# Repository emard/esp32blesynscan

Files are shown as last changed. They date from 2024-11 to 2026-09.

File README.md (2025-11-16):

# ESP32 blesyncscan

Micropython ESP32, ESP32S3, ESP32C3 Bluetooth Low Energy (BLE)
Motor server, WiFi Motor Server and USB-WiFi Motor Client for
SynScan Pro on Windows, Linux, Android.
Arduino ESP32 Bluetooth Classic UART bridge for SynScan Pro
under Wine on Linux.
UART 3.3V TTL is connected to SkyWatcher Virtuoso Mini
or Virtuoso GTi mount.

ESP32C3 USB-C port can be used as direct USB-SERIAL on PC
connected to Motor over wire or remote USB-SERIAL over WiFi.

Do not use this to upgrade Motor firmware.
Motor firmware should be upgraded over wire using
USB-SERIAL UART 3.3V TTL based on PL2303 or FT232R chip.

# Install

"micropython" directory contains latest developent.
To install, continue with micropython/README.md

"Arduino" directory contains old code which should be
upgraded with features micropython code has.
To install, continue with Arduino/README.md

Bluetooth Classic is available only for Arduino.
Micropython doesn't support Bluetooth Classic.

# Electrical

There should be 12V->3.3V converter.
To save power recommended is switching converter 
(Canton Power or RECOM).
RJ-12 plug can't guarantee that GND makes
connection before 12V pin. Hot-plugging
can apply 12V to 3.3V pins and risk a
permanent damage. Avoid hot-plugging.

On the mount "Virtuoso Mini" RX and TX are labeled
swapped and seems as wired together making it a
half-duplex serial port and ESP32 should cancel echo.
ESP32 TX line should "simulate" open collector
output with a resistor 10k and small low drop diode
BAT42.

On the mount "Virtuoso GTi" RX and TX are labeled
normal and are not wired together making it a
full-duplex serial port without echo.
ESP32 TX line should connect directly to ESP32.

In the mount manual see RJ-12 pinout.
Conenct RJ-12 RX/TX with short straight
RJ-12 cable to ESP32 RX2/TX2 pins.

# Schematics

First prototype (ESP32)

                 Canton Power
                ┌─────────────┐
                │IN        OUT│
                │12V  GND 3.3V│
                └─────────────┘
                  │    │    │
      MOUNT       │    │    └───────────────┐
     MINI/GTi     │    │                    │   ESP32
    ┌───────┐     │    │                    │  ┌───────┐
    │    12V│─────┘    │         10k/BAT42  └──│3.3V   │
    │       │          │         ┌─░░░░─┐      │       │
    │     TX│──────────│─────────┼──>∫──┴──────│TXD    │
    │       │          │         └─────────────│TX     │
    │     RX│──────────│───────────────────────│RX     │
    │       │          │                       │       │
    │    GND│──────────┴───────────────────────│GND    │
    └───────┘                                  └───────┘

Minimal schematic (ESP32S3) old

                     RECOM
                 R-78K3.3-0.5
                ┌─────────────┐
                │12V  GND 3.3V│
                │IN        OUT│
                └─────────────┘
                  │    │    │
      MOUNT       │    │    └─────────┐
     MINI/GTi     │    │              │   ESP32S3
    ┌───────┐     │    │              │  ┌───────┐
    │    12V│─────┘    │   10k/BAT42  └──│3.3V   │
    │       │          │    ┌─░░░░─┐     │       │
    │     TX│──────────│────┼──>∫──┴─────│TXD    │
    │       │          │    └────────────│TX     │
    │     RX│──────────│─────────────────│RX     │
    │       │          │                 │       │
    │    GND│──────────┴─────────────────│GND    │
    └───────┘                            └───────┘

Minimal schematic (ESP32S3) new

                     RECOM
                 R-78K3.3-0.5
                ┌─────────────┐
                │12V  GND 3.3V│
                │IN        OUT│
                └─────────────┘
                  │    │    │
      MOUNT       │    │    └─────────┐
     MINI/GTi     │    │              │   ESP32S3
    ┌───────┐     │    │   10k/BAT42  │  ┌───────┐
    │    12V│─────┘    │    ┌─░░░░─┐  └──│3.3V   │
    │       │          │    ├──>∫──┴─────│TXD    │
    │     TX│──────────│────┴────────────│TX     │
    │       │          │    ┌─░░░░─┐     │       │
    │     RX│──────────│────┼──>∫──┴─────│RXD    │
    │       │          │    └────────────│RX     │
    │    GND│──────────┴─────────────────│GND    │
    └───────┘                            └───────┘

part numbers and pinouts

    RJ-11 or RJ-12 Connector
    Mouser P/N: 538-95501-2661   0.5$
    Mouser P/N: 523-RJE031660310 1$
    Mouser P/N: 490-CRJ051-1-TH  2$

      RJ-12         RJ-11
    ┌────────┐    ┌────────┐
    │ 123456 │    │  2345  │
    │        │    │        │
    └──┐  ┌──┘    └──┐  ┌──┘
       └──┘          └──┘
    front view    front view

    1        N.C.
    2 yellow TX       (3.3V) (esp32 sends to "Mini", receives from "GTi")
    3 green  Vpp+     ( 12V) (esp32 draws power)
    4 red    RX       (3.3V) (esp32 receives from "Mini", sends to "GTi")
    5 black  GND
    6        N.N.

    Voltage converter 4.5-36V -> 3.3V
    Mouser P/N: 919-R-78K3.3-0.5 7$

                     RECOM 
                 R-78K3.3-0.5
                ┌─────────────┐
             IN │12V  GND 3.3V│ OUT
                │             │
                │             │
                └─────────────┘
                  bottom view

    XIAO ESP32S3 MINI old
    Mouser P/N: 713-113991114    7$

                 XIAO  ESP32S3
                ┌─────────────┐
                │1    USB   5V│
                │2         GND│
                │3        3.3V│
                │4           9│
                │5           8│
                │6  TX       7│
                │43 TXD  RX 44│
                └─────────────┘
                    top view

    XIAO ESP32C3 MINI old
    Mouser P/N: 713-113991054    5$

                 XIAO  ESP32C3
                ┌─────────────┐
                │2    USB   5V│
                │3         GND│
                │4        3.3V│
                │5          10│
                │6           9│
                │7  TX       8│
                │21 TXD  RX 20│
                └─────────────┘
                    top view

    XIAO ESP32S3 MINI new
    Mouser P/N: 713-113991114    7$

                 XIAO  ESP32S3
                ┌─────────────┐
                │1    USB   5V│
                │2         GND│
                │3        3.3V│
                │4           9│
                │5           8│
                │6  TXD  RXD 7│
                │43 TX   RX 44│
                └─────────────┘
                    top view

    XIAO ESP32C3 MINI new
    Mouser P/N: 713-113991054    5$

                 XIAO  ESP32C3
                ┌─────────────┐
                │2    USB   5V│
                │3         GND│
                │4        3.3V│
                │5          10│
                │6           9│
                │7  TXD  RXD 8│
                │21 TX   RX 20│
                └─────────────┘
                    top view

# Connection

Looking at female RJ-12 socket on the mount:

    ┌────────┐
    │ 123456 │
    │        │
    └──┐  ┌──┘
       └──┘

    1 blue   N.C.
    2 yellow TX       (3.3V) (mount "Mini" receives, "GTi" sends)
    3 green  Vpp+     ( 12V) (mount provides power)
    4 red    RX       (3.3V) (mount "Mini" sends, "GTi" receives)
    5 black  GND
    6 white  Reserved (3.3V)

RX/TX roles on the mount "Virtuoso Mini" are swapped and
actually indicate RX2/TX2 on ESP32.

    Virtuoso Mini  ESP32
    -------------  ----------
    2 yellow TX    TX2 GPIO17 (over resistor/diode)
    4 red    RX    RX2 GPIO16
    5 black  GND   GND

RX/TX roles on the mount "Virtuoso GTi" are labeled normal,
here we swap TX2/RX2 on ESP32.

    Virtuoso GTi   ESP32
    ------------   ----------
    2 yellow TX    RX2 GPIO17 (direct)
    4 red    RX    TX2 GPIO16
    5 black  GND   GND

RJ-11 4-pin socket can be used instead of
RJ-12 6-pin because pins 1 and 6 are not connected.

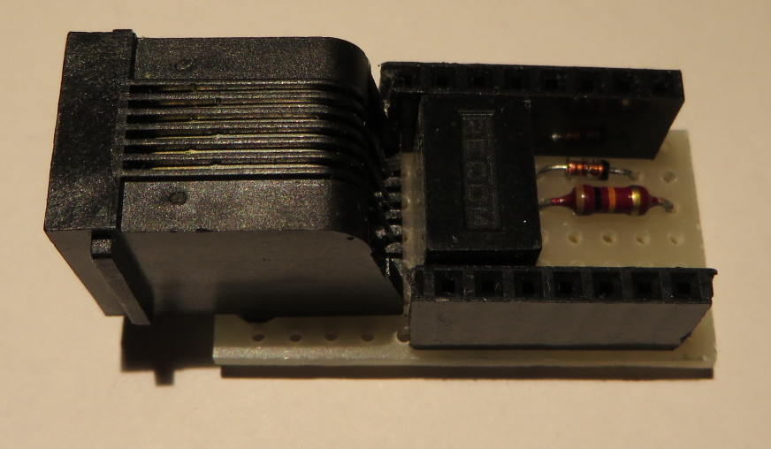
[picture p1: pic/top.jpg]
top


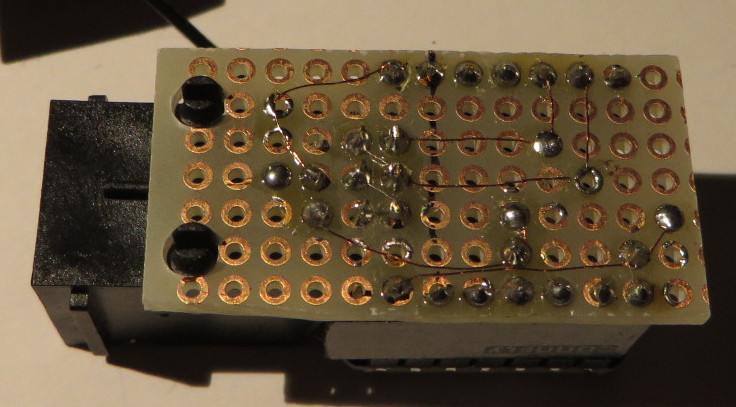
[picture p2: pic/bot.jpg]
bot


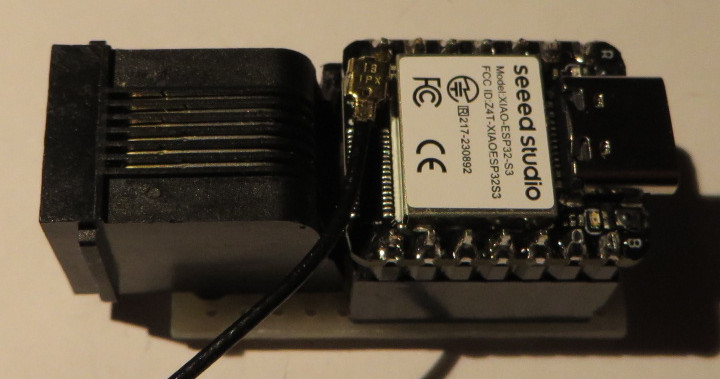
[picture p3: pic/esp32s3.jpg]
esp32s3


# WARNING WARNING WARNING

RJ12 pinout on the adapter matches the pinout
on the mount, so the "straight" wired cable
should be used.

There are different RJ-11 and RJ-12 cables,
with [straight and cross wiring](/doc/straight-vs-cross-cable.pdf).
For the telephones it does not matter but here it matters!

STANDARD PHONE CROSS CABLE MAY NOT BE SUITABLE.
USE ONLY STRAIGHT WIRED 4-PIN RJ-11 or
STRAIGHT WIRED 6-PIN RJ-12. CROSS RJ-11 AND RJ-12 
CABLES AND ALL 2-PIN RJ-11 CABLES ARE NOT SUITABLE.
IF A CROSS WIRED CABLE OR ANY 2-PIN CABLE IS CONNECTED
THEN 12V WILL FRY ELECTRONICS IN THE MOUNT AND ESP32.

# Bluetooth Classic or Low Energy

After board power ON or reset by pressing "EN" button,
blue LED will turn ON for 1.5 seconds.

By default if nothing is pressed ESP32 provides
Bluetooth Low Energy Serial.

If "BOOT" button is held during blue LED is ON
then ESP32 will provide Bluetooth Classic Serial.

ESP32 in Bluetooth Low Energy mode only supports
BLE protocol and does not save battery power.
In both Classic and Low Energy modes ESP32 consumes
about 70 mA.

# Android

Synscan works in BLE mode.

SynScan pro -> Settings -> Connection Settings -> BLE

If device no longer appears in connect list and 
you want to retry connecting, then android application
has to be stopped and started again:

View applications as smaller windows. To stop SynScan,
drag it left on ardoid 10 or drag it up on android 14.

Protocol testing:

"Serial Bluetooth Terminal" can connect in
Bluetooth Classic directly when ESP32 is booted
in Bluetooth Classic mode.

"Serial Bluetooth Terminal" can connect in
Low Energy mode with long touch on SynScan_BLE device
selecting "Edit" Custom profile and then
accepting offered UUID values for Service, Read and Write.
Settings:

    Receive Newline = CR
    Send    Newline = Auto (Same as Receive)
    Send    Local Echo ( o) enabled

Basic request/response works:

    request
    :e1\r

    response
    =0210A1\r

# Linux Bluetooth Classic

Bluetooth classic works from linux and
SynScan 2.5.2 pro running under wine,
connecting as serial port.

in shell 1

    hcitool scan
    Scanning ...
            24:0A:C4:11:22:33   SynScan_BT
    rfcomm bind /dev/rfcomm0 24:0A:C4:11:22:33
    unzip synscanpro_windows_252.zip
    cd SynScanPro
    wine SynScanPro.exe
    ... wine will initialize com1 as symlink to /dev/ttyS0
    ... we must change this symlink to /dev/rfcomm0

in shell 2

    cd ~/.wine/dosdevices
    ln -sf /dev/rfcomm0 com1

in SynScan Pro window 

    ... SynScan pro -> Settings -> Connect Settings -> Serial
    ... Serial Port: COM1
    ... press top "<" touch btn then "Connect" btn will appear.
    ... touch "Connect" btn, retry few times

SynScanPro can be debugged from wine:

    winedbg --gdb SynScanPro.exe
    ...
    Wine-gdb> c

# Linux Bluetooth Low Energy

Bluetooth low energy works from linux and
SynScan 2.5.2 pro running under wine,
connecting as serial port.

It works over ble-serial if esp32 is emulating
BLE nRF chip. RN4871 chip emulation will not be
detected by ble-serial.

Install
    
    https://github.com/Jakeler/ble-serial

in shell 1

    source ble-venv/bin/activate
    ble-scan -i hci1
            24:0A:C4:11:22:33   SynScan_BLE
    ble-serial -i hci1 -d 24:0A:C4:11:22:33
    (ble-venv) guest@nuc1:~$ ble-serial -i hci1 -d 24:0A:C4:11:22:33
    23:38:03.521 | INFO | linux_pty.py: Port endpoint created on /tmp/ttyBLE -> /dev/pts/2
    23:38:03.521 | INFO | ble_interface.py: Receiver set up
    23:38:03.741 | INFO | ble_interface.py: Trying to connect with 24:0A:C4:11:22:33: SynScan_BLE
    23:38:05.443 | INFO | ble_interface.py: Device 24:0A:C4:11:22:33 connected
    23:38:05.443 | INFO | ble_interface.py: Found write characteristic 6e400002-b5a3-f393-e0a9-e50e24dcca9e (H. 44)
    23:38:05.443 | INFO | ble_interface.py: Found notify characteristic 6e400003-b5a3-f393-e0a9-e50e24dcca9e (H. 41)
    23:38:05.826 | INFO | main.py: Running main loop!

in shell 2

    cd SynScanPro
    wine SynScanPro.exe
    ... wine will initialize com1 as symlink to /dev/ttyS0
    ... we must change this symlink to /dev/rfcomm0

in shell 3

    cd ~/.wine/dosdevices
    ln -sf /tmp/ttyBLE com1

in SynScan Pro window 

    ... SynScan pro -> Settings -> Connect Settings -> Serial
    ... Serial Port: COM1
    ... press top "<" touch btn then "Connect" btn will appear.
    ... touch "Connect" btn, retry few times

SynScanPro can be debugged from wine:

    winedbg --gdb SynScanPro.exe
    ...
    Wine-gdb> c

# Windows

With suitable BLE adapter, for example TP-LINK UB500
SynScan pro 2.5.2 for windows connects with "SynScan_BLE".

"SimplySerial" is simple terminal emulator for
windows. It can can be started from powershell
to print debug messages from esp32.

    ./ss -com:8 -baud:9600
    Connected
    Disconnected

# Principle of operation

ESP32 creates a bluetooth server with serial port bridge.
Phyisical TTL serial port should be 9600,8,n,1. Using 9800
baud seems to receive less noise than 9600 baud.

Minimum that works is a BLE Service (UUID 0xA002) with
two characteristics, one for RX other for TX:

RX Direction SynScan->motor (UUID 0xC302)

Bluetooth LE packetizes serial protocol so
entire message is delivered in one packet.
ESP32 filters out some problematic commands for
"2.16.A1" motor firmware (see Firmware bugfix)
other firmwares may not need it.
Message is written to TTL serial and signaled
with "NOTIFY" flow control.

TX Direction motor->SynScan (UUID 0xC306)

TTL serial receiver buffers bytes until "complete"
message is received, it begins with '=' or '!'
and ends with '\r'. It is delivered via bluetooth
and signaled with "INDICATE" flow control.

# TTL Serial Port

Mount's serial TTL port is half-duplex
and it seems that mount has hardware
loopback. So everything that esp32 sends
to the mount, the mount immediately echoes it.

In the code there is echo cancellation built in
to reduce BLE traffic, run faster and save energy.

Mount and ESP32 cannot send at the
same time. If ESP32 tries to send
while mount sends, then the data
received by ESP32 will be just noise.

Received bytes are occasionaly wrong
with typically one of the bits that
should be 0 errorenously received as 1.
This happens less often when mount is
just powered one and more often after
alignment when mount is driving motors
for tracking.

# Firmware bugfix

Motor firmware version 2.16.A1 is the latest but has
problem with SynScan application on android.
After each connect user must enable "Auxiliary Encoder"
otherwise mount will start turning around azimuth axis
and will never stop by itself (user should press cancel to stop).

According to
[BDN at Cloudy Nights](https://www.cloudynights.com/topic/941083-skywatcher-heritage-90-virtuoso-synscan-pro-compatibility/)
this bug can be fixed by making USB-SERIAL adapter and flashing firmware
[MC006_Tracking_V0216.MCF](https://stargazerslounge.com/topic/336944-firmware-for-the-virtuoso-skywatcher/)
posted by Antoine1997 at Stargazer's Lounge.

Although this firmware also has version 2.16.A1 it
is different and fixes the encoders problem. Warning
flashing firmware using WiFi dongle will brick the board and
should never be tried, so use only usb-serial.

If you are not comfortable with flashing the firmware,
here is the fix that forces using Auxiliary encoders.

fix#1: in function "udpcb()" one message is rewritten
with this fix Auxiliary Encoder doesn't have to be enabled.
It seems that mount internally always uses Auxiliary Encoders.
Regardless of Auxiliary Encoders being set ON or OFF without
this patch, when clutches are released and mount is manually moved,
SynScan always knows its new position.

    :W2050000\r -> :W2040000\r

fix#2: prevents sending junk to motor firmware which
is easy to crash.

SynScan sends some AT command probably for its
original SynScan WiFi ESP8266 AT firmware.
This AT command should not reach motor firmware so
"udpcb()" function rewrites this AT command as ":e1\\r"
and to this command motor firmware responds with
version number which is not really response to AT
command but SynScan accepts it.

    AT+CWMODE_CUR?\r\n -> :e1\r

fix#3: receive buffer is discarded after timeout of 10 ms
or when unexpected (noise) byte is received outside of
expected chars "=0123456789ABCDEF!\r". Synscan will
retry the command after its own timeout.
This fix improves initial connect, without this fix
and without open collector fit with diode and resistor,
SynScan sometimes needs to be manually restarted few
times to connect.

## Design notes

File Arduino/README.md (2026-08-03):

# Install

"esp32/btblesynscan" supports both Bluetooth
Classic and Bluetooth Low Energy on ESP32.
"esp32s3" supports Bluetooth Low Energy on ESP32S3.

From board manager Install esp32 by espressif.
Select board "ESP32 Dev Module" or "XIAO_ESP32S3".

Copy "btblesynscan.ino" to directory "~Arduino/esp32blesynscan/btblesynscan/btblesynscan.ino"
Copy "esp32s3.ino" to directory "~Arduino/esp32blesynscan/esp32s3/esp32s3.ino"

From Arduino, open project "~/Arduino/esp32blesynscan/btblesynscan",
or "~/Arduino/esp32blesynscan/esp32s3"
compile and upload to ESP32 board connected with Micro USB Cable (ESP32)
or USB-C Cable (ESP32S3).

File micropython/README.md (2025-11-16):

# SynScan_BLE Micropython version

300 lines of micropython replace
parts of synscan protocol on transmit
and receive side to:

Slow speed for encoders to reliably
track position without loosing counts.

Fine tune counts per revolution.
Turning both axes for 180° should
point to the same object as 0°.

Fake version number for synscan
to avoid using long X-commands.

# Install

    mpremote cp synscan_cfg.py synscan.py main.py :/

# Configure

Almost everything is configurable. Edit

    synscan_cfg.py

Using your favourite text editor on PC.
ESP32 has good editor written in micropython.

# Onboard Editor

ESP32 can run small [VT100 terminal editor](https://github.com/robert-hh/Micropython-Editor)

Automatic install from internet using mpremote mip:

    mpremote mip install github:robert-hh/Micropython-Editor

Edit config file:

    >>> from pye import pye
    >>> pye("synscan_cfg.py")

quick editor help

    ctrl-q        quit
    ctrl-s        save
    backspace     delete left of cursor
    arrows        move cursor
    shift-arrows  select block
    del           delete selected block
    ctrl-c        copy   selected block
    ctrl-v        paste  selected block
    ctrl-e        redraw screen

Troubleshooting

ESP32-WROOM and ESP32C3 dont have PSRAM so
memory is tight. After "import synscan"
there will be not enough free memory to
load editor:

    >>> from pye import pye
    Traceback (most recent call last):
      File "<stdin>", line 1, in <module>
    MemoryError: memory allocation failed, allocating 285 bytes

workaround: Get micropython prompt with ctrl-c, then
while holding ctrl type quickly "dccc" to soft reboot
and immediately interrupt "main.py" before
"import synscan". It should be possible to
load editor then:

    ctrl-c
    ...
    >>>
    ctrl-dccc
    ...
    >>> from pye import pye
    >>> pye("synscan_cfg.py")

# BLE Motor Server

Primary use is for Android. Works on Windows.
Linux BLE-serial written in python doesn't work.
Mount lacks BLE support and using its WiFi
is not practical, complicated routing etc.

BLE connects in few seconds, works stable and reliable.
WiFi on android is free to be used for internet
access or camera.

Works on ESP32, ESP32S3, ESP32C3.

When BLE receives request from synscan,
it sends it over UART and waits some timeout 30 ms or 200 ms
for UART response. Received response
is sent back to synscan. 

UART should send someting to motor hardware
to get response. Motor hardware is otherwise quiet.

# WiFi Motor Server

Primary use is to make additional networking
connectivity and compatibility. It can be WiFi
client while mount is WiFi Server.

Works on ESP32, ESP32C3.

To print IP

    synscan.wifi.ifconfig()

Currently it doesn't work reliable on ESP32S3.
Multiple retries required to connect. Packet loss
and timeout too long to be practical (30 seconds).

# WiFi to USB-Serial Motor Client

Primary use is for linux. Works on Windows and Android too.
Linux BLE-serial written in python doesn't work so this USB
to WiFi bridge is very practical.
ESP32 connects to mount using WiFi
and modifies protocol to fix issues.

Works on ESP32, ESP32S3, ESP32C3 (wine reboots ESP32C3).
Micropython versions from 1.23.0 to 1.26.1 have been
tried but ESP32S3 doesn't connect to WiFi.

Android: SynScan Pro connects with default serial settings

    SynScan Pro > Settings > Connection Settings > Serial

Linux: SynScan Pro works under wine when you find COM port
and set serial read timeout to 3-5 seconds.

To find out which serial port on wine is for synscan:

    ls -al ~/.wine/dosdevices
    lrwxrwxrwx 1 user user   12 Oct  10 23:52 com5 -> /dev/ttyACM0

Port is COM5 (last number can vary).

Wine SynScan Pro needs increased serial parameters to connect:

    Resend Tries * Serial Read Timeout > 9 seconds

ESP32S3 connects with default serial timeouts.

ESP32C3 needs increased serial timeouts.
When Synscan initiates connection to serial port it
probably toggles DTR or does something to serial port
which causes ESP32C3 to restart.
Read timeout should be long enough for
ESP32C3 to boot and connect to mount WiFi.

    SynScan Pro > Settings > Connection Settings > Serial
    SynScan Pro > Settings > Connection Settings > Resend Tries      > 2
    SynScan Pro > Settings > Connection Settings > Read Timeout (ms) > 5000

or

    SynScan Pro > Settings > Connection Settings > Serial
    SynScan Pro > Settings > Connection Settings > Resend Tries      > 10
    SynScan Pro > Settings > Connection Settings > Read Timeout (ms) > 1000

# Direct Wire USB-Serial Motor Client

Works on Windows, Android, Linux.
Works on ESP32, ESP32S3, ESP32C3 (wine reboots ESP32C3).
Similar as WiFi to USB-Serial Motor Client.

# Troubleshooting

Virtuoso Mini with MC006:

According to
[BDN at Cloudy Nights](https://www.cloudynights.com/topic/941083-skywatcher-heritage-90-virtuoso-synscan-pro-compatibility/)
this bug can be fixed by making USB-SERIAL adapter and flashing firmware
[MC006_Tracking_V0216.MCF](https://stargazerslounge.com/topic/336944-firmware-for-the-virtuoso-skywatcher/)
posted by Antoine1997 at Stargazer's Lounge.

Virtuoso GTi with MC014:

Flash firmware 3.40.AF but and synscan_cfg.py has
appropriate fixes, this includes slowing down manual
and goto slew, adjusting number of pulses per revolution
and rewriting firmware version to 3.36.AF to avoid using
of new X-commands.

CPU of MC014 misses encoder pulses, it is probably because
interrupt is used to count pulses instead of using hardware
counting like PCNT on ESP32 which may also be available on ESP8266.
which is mounted on MC014 PCB.

Best is to avoid switching to aux controllers during first 15 minutes,
while WiFi LED on the mount is blinking.
After 15 minutes WiFi LED will turn ON constantly, WiFi will be
off and interrupts will have more chance to catch encoder pulses.
so then it is good time to try aux encoders.

Encoders will then correctly work when synscan commands are send
from application to the mount and mount is moving slow according
to synscan_cfg.py slew speed setup.

But when clutches are released for manually pointing telescope
aka "Freedom Find" mode then aux controllers will start
loosing counts and that means that "Freedom Find" actually
doesn't work for MC014 hardware with currently tried firmwares
3.36.AF and 3.40.AF.

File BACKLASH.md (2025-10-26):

# Backlash Reduction

Backlash is annoying accumulated mechanical energy
in motor tranmission which visually manifests as
telescope first goes a few arc minutes in counter
direction than it goes in correct direction.

Backlash can be reduced to be almost visually
unnoticeable by precisely adjusting distance
between worm and sprocket wheel.

Tools required:

    Phillips screwdriver PH1
    Flat long screwdriver
    L-shaped Hex Allen wrench 2 mm
    Fork-shaped Hex nut wrench 7 mm

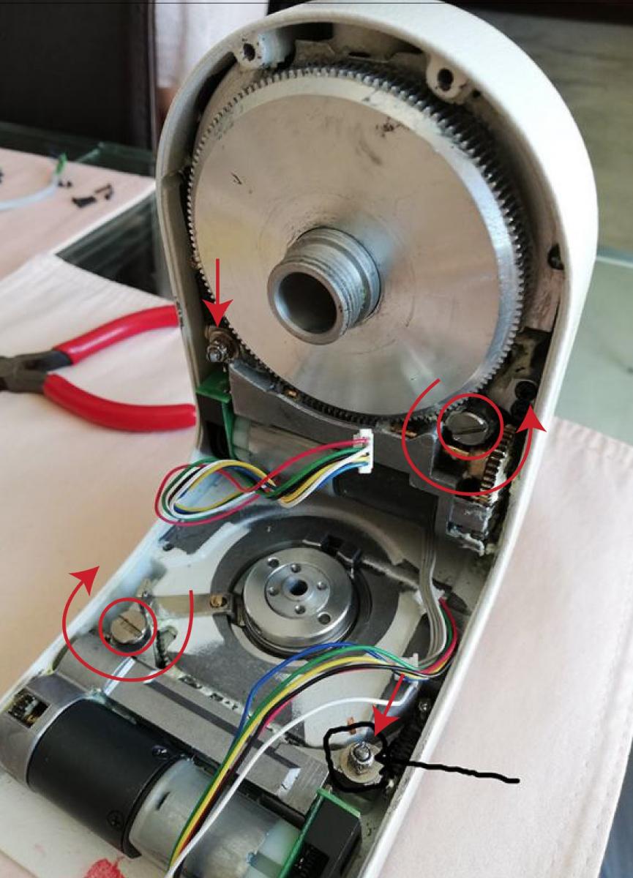
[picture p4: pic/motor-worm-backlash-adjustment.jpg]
backlash


Backlash can be adjusted by minimal disassembly,
no wires need to be removed but hood has to be
released carefully and held by hands while unscrewing
big screws while being very gentle with wires.

With long flat screwdriver release the big cylindrical
flat screw by turning 180° counter-clockwise.
On the picture this flat screw is marked by red circle.

Not visible on the picture is a smaller black screw
touching the big screw, this screw has hex hole for
2 mm Allen wrench and is fixed in place by counter-tightened
7 mm nut which is additionaly fixed with lacquer.

With Hex Fork wrench and Hex Allen wrench break the
lacquer and release hex nut to allow some space for
adjustment, like 1 mm.

Partially assemble the mount to leave hood open for
access with Hex Allen wrench and to have neccesary
parts in place to hold the telescope tube. Launch
motor control software, set software backlash
correction to zero and use cursors to move telescope
by visually monitoring backlash.

Change distance of the worm from sprocket wheel
by turning the black screw with Hex Allen wrench
until backlash disappears.

That,s it! After carefully tightening and assembling
check that everying is still working.

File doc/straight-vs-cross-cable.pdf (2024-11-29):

For cables with RJ-11 connectors, the terminology “Straight-through” and “Reverse” are often confused.

When one of these cables is considered “straight-through”, it means that when looking at both connectors side-by-side, the colors of the internal wires match (as shown below).

This is often mistaken as “straight-through”, mainly due to fact that if you were to stretch the cable out, the wires would stay side by side the whole length without going over each other. This, however, is incorrect.

For telephone systems, this doesn’t make a difference. However, when these cables are used for other means, such as personal projects, in various nonstandard uses, or other DIY-type instances, this difference is often important.

When it is “reverse,” however, the wires are mirrored (as shown below).

non-standard

standard

## RJ-11 CONNECTOR STRAIGHT-THROUGH (non-standard) vs. REVERSE (standard) EXPLANATION

(Hook is underneath)

RJ11 Plug

(Hook is underneath) (Hook is underneath)

RJ11 Plug

(Hook is underneath) (Hook is underneath)

(Hook is underneath)

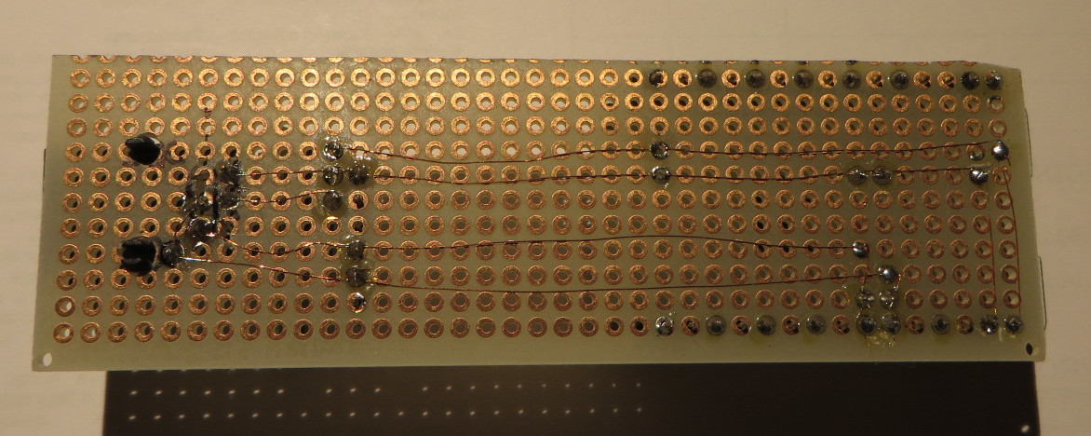
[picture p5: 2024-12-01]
pic/prototype-bot.jpg

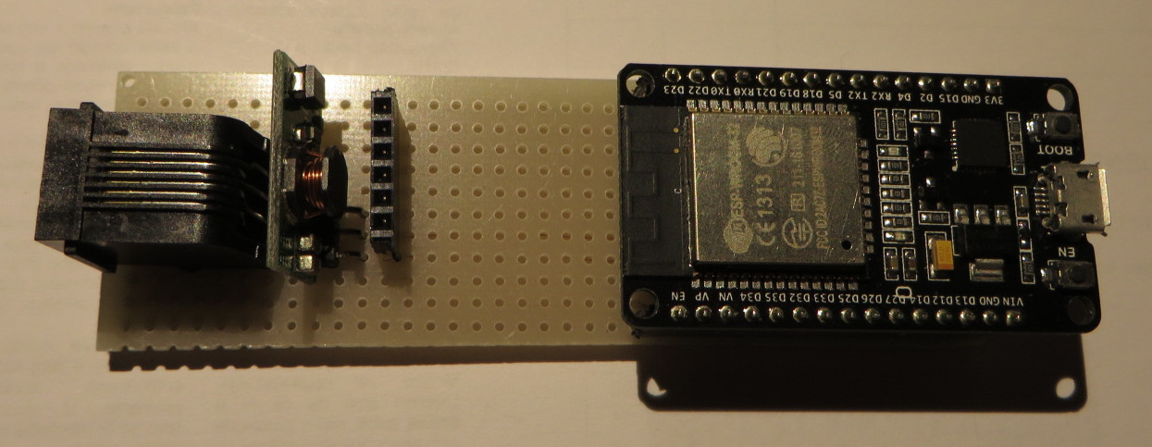
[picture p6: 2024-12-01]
pic/prototype-top.jpg

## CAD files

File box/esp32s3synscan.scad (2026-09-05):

// box to insert pcb and fix with 2 screws

pcb_size = [19,41,1.6]; // size of PCB

box_inner = [22,42,21+2.5];
thick = 2;

rail_top   = [2,42,2];
rail_bot   = [2.5,42,2];
rail_spc   = 2.5;

pcb_bottom = 2.5+3; // space from bottom
usb_pos = 14; // from PCB bottom

module pcb()
{
  translate([0,-thick,box_inner[2]/2-rail_bot[2]/2-pcb_bottom])
  cube(pcb_size,center=true);
}

module rounded_cube(v,r)
{
  minkowski()
  {
    h_minkowski=0.01;
    cube(v-[2*r,2*r,h_minkowski],center=true);
    cylinder(h=h_minkowski,r=r,$fn=90,center=true);
  };
}

module rail_old()
{
  difference()
  {
    cube(rail_outer,center=true);
    cube(rail_inner,center=true);
  }
}

module rail(i)
{
  translate([-i*rail_bot[0]/2,(rail_bot[1]-box_inner[1]-thick)/2,rail_bot[2]/2+rail_spc/2])
    cube(rail_bot,center=true);
  translate([-i*rail_top[0]/2,(rail_top[1]-box_inner[1]-thick)/2,-rail_top[2]/2-rail_spc/2])
    cube(rail_top,center=true);
}

module rails()
{
  for(i=[-1,1])
    translate([(box_inner[0]/2)*i,0,box_inner[2]/2-rail_bot[2]/2-pcb_bottom])
      rail(i);
}

// not used
module usb_connector_cut()
{
  translate([0,-box_inner[1]/2,+box_inner[2]/2-pcb_bottom-usb_pos])
  cube([31,10,6],center=true);
}

module rj12_connector_cut_rear()
{
  translate([0,box_inner[1]/2,+box_inner[2]/2-pcb_bottom-8.5])
  cube([15,10,14],center=true);
}

module rj12_connector_cut_side()
{
  translate([0,box_inner[1]/2-10,+box_inner[2]/2-pcb_bottom-16])
  cube([13,16,10],center=true);
}

// not used - can't screw thru antenna
module screw_holes()
{
  for(i=[-1,1])
  translate([i*2.54*3,box_inner[1]/2-6,box_inner[2]/2])
    cylinder(d=1.8,h=10,$fn=16,center=true);
}

module box()
{
  difference()
  {
    cube_dim=box_inner+[2,1,2]*thick;
    rotate([90,0,0])
    rounded_cube([cube_dim[0],cube_dim[2],cube_dim[1]],r=3);
    translate([0,-thick,0])
    cube(box_inner,center=true);
    // usb_connector_cut();
    rj12_connector_cut_rear();
    //rj12_connector_cut_side();
    // screw_holes();
  }
  rails();
}

box();
%pcb();

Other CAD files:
box/esp32s3synscan2.scad
box/esp32synscan.scad

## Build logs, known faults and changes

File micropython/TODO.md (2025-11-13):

# TODO

    [x] after disconnect, LED stays ON
    [ ] periodically check uart and autodetect
        if no response
    [x] instead of if/then use dictionary rewrite
        for command and response
    [x] fix half/full duplex autodetection
    [ ] wifi client, log udp traffic to find what is problem
    [ ] W10D8004: W20D8004: are motor power off commands
        no answer to :f1
    [ ] works if timeout set to 2200 ms or higher
    [ ] half/full duplex wrong detection when USB is plugged
        first and then mount powered up
        steps to reproduce
        android and virtuoso mini
        power off mount, plug usb to android,
        power on mount, connnect, goto 10 deg,
        mount will stop responding
        on upper right corner of android circle will start rotating
        further reconnect is not possible because
        android causes something for micropython to exit input loop
        back to repl prompt
        to verify this
        keep mount powered, unplug android, plug PC usb
        mpremote
        press enter and see repl (while it shouldnt)
        >>>
        temporary fix is to force half duplex in synscan_cfg.py
        UART_INIT = [uart_half_duplex]
    [ ] usbserial resets esp32c3
    [ ] if motor server then
        from timer call wire_autodetect() until mount responds

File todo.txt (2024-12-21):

[ ] allow to change MAC address
[ ] inclue MAC address in BLE name
[ ] usb-serial function

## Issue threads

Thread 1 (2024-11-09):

Works in terminal but synscan pro doesn't find the device

emard, 2024-11-09:
Currently it works in serial terminal but
synscan pro on android 10 doesn't find the
BLE device.

Maybe it would work if correct bluetooth
device name and UUID are set, similar but
different than this

    #define BLE_NAME "SynScan"
    #define SERVICE_UUID           "6E400001-B5A3-F393-E0A9-E50E24DCCA9E"  // UART service UUID nordic nRF
    #define CHARACTERISTIC_UUID_RX "6E400002-B5A3-F393-E0A9-E50E24DCCA9E"
    #define CHARACTERISTIC_UUID_TX "6E400003-B5A3-F393-E0A9-E50E24DCCA9E"

If someone has some suggestion please help.

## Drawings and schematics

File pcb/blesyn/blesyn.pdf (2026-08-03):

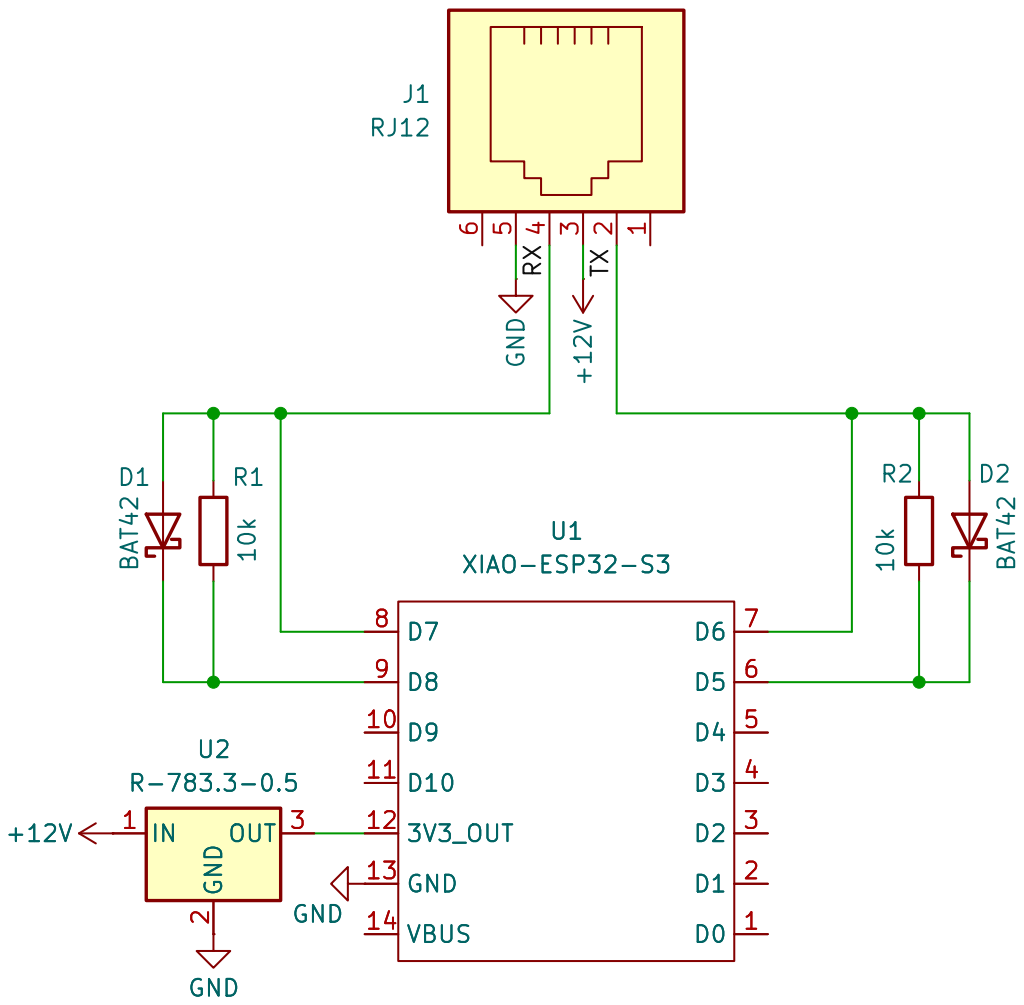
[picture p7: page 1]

Size: A4 | Rev: 1.0
KiCad E.D.A. 10.0.4 | Id: 1/1

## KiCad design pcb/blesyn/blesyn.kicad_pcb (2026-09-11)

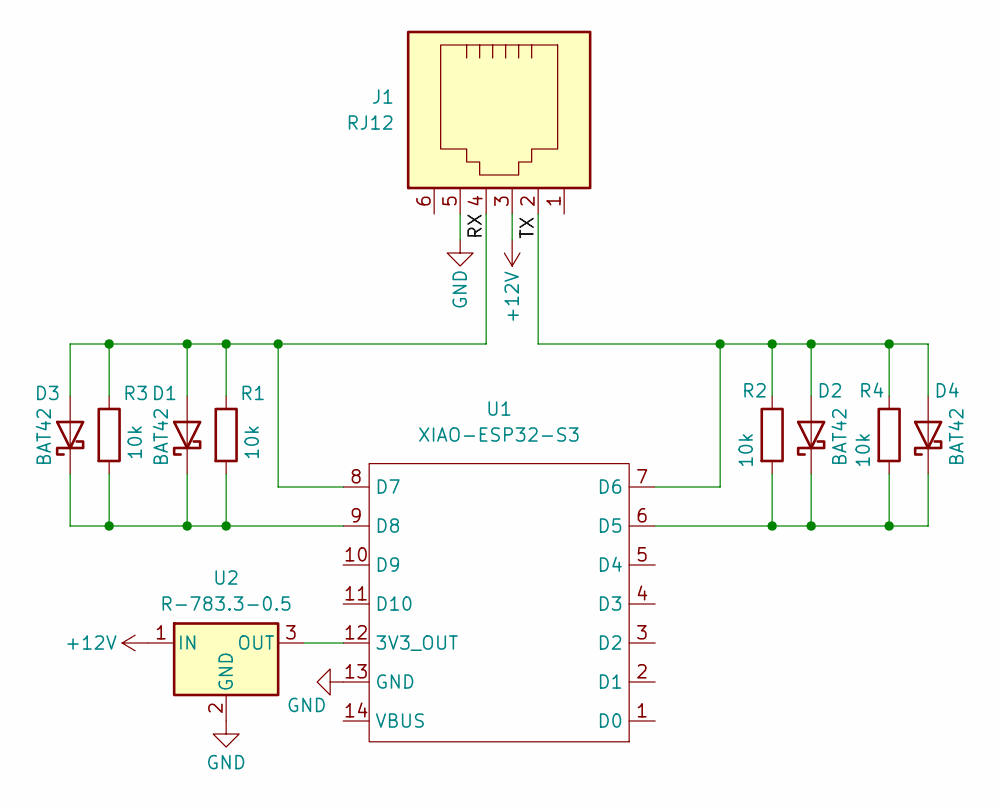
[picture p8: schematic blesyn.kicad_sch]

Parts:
D1, D2: BAT42; D_DO-34_SOD68_P7.62mm_Horizontal
D3, D4: BAT42; D_1206_3216Metric_Pad1.42x1.75mm_HandSolder
J1: RJ12; RJ12_Amphenol_54601-x06_Horizontal
R1, R2: 10k; R_Axial_DIN0207_L6.3mm_D2.5mm_P10.16mm_Horizontal
R3, R4: 10k; R_1206_3216Metric_Pad1.30x1.75mm_HandSolder
U1: XIAO-ESP32-S3; XIAO-ESP32-S3-DIP
U2: R-783.3-0.5; Converter_DCDC_RECOM_R-78E-0.5_THT

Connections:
+12V: J1.3, U2.1 (IN)
/RX: D1.2 (A), D3.2 (A), J1.4, R1.1, R3.1, U1.8 (D7)
/TX: D2.2 (A), D4.2 (A), J1.2, R2.1, R4.1, U1.7 (D6)
GND: J1.5, U1.13 (GND), U2.2 (GND)
unnamed: D1.1 (K), D3.1 (K), R1.2, R3.2, U1.9 (D8)
unnamed: D2.1 (K), D4.1 (K), R2.2, R4.2, U1.6 (D5)
unnamed: U1.12 (3V3_OUT), U2.3 (OUT)

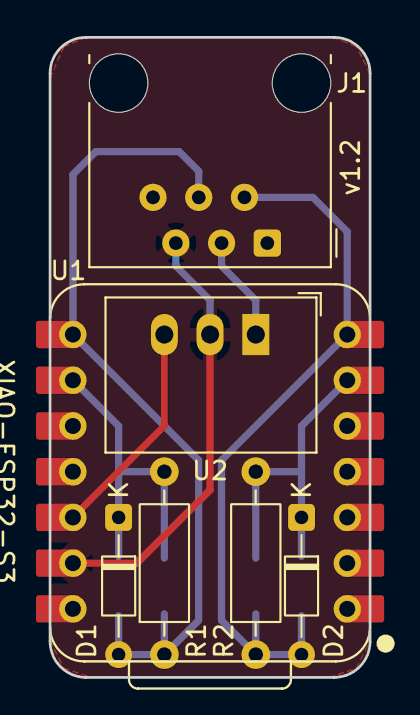
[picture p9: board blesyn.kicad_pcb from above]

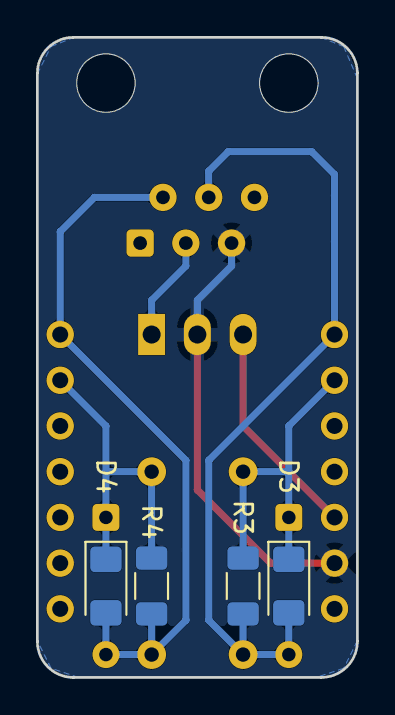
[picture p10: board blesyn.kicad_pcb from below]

Board: 2 copper layers, 17.8 x 35.6 mm, 11 parts (4 on the bottom side), 7 nets.

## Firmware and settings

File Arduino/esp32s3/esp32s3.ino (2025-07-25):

// install Board -> Boards Manager -> "esp32 by espressif"
// Board: XIAO_ESP32S3
// CPU freq 80MHz (WiFi/BT) for power saving

/*********** COMMON ***********/

// Hardware Serial2 pins
#define RXD2 44
#define TXD2 43
#define BAUD 9600

// [us] USB read time (throttle fast usb-serial, 1042 us = 9600 baud, 0 disable)
#define USB_RX_CHAR_US 0
// [us] RJ-12 discard packets coming faster on Serial2.write, 0 disable
#define RJ12_TX_PACKET_US 0

// [us] timeout on RJ12 receive, reset txbuf buffer
#define RJ12_RX_TIMEOUT_US 60000000
// [us] timeout on USB receive, reset rxbuf buffer
#define USB_RX_TIMEOUT_US 60000000

// TXBUF_LEN 0  to disable
// TXBUF_LEN > 0 to enable (TX_INDICATE needs it)
// recommend TXBUF_LEN 32 with TX_INDICATE 1
// [bytes] length of TX buffer
// conditions when buffer is delivered
// with optional notify/indicate signal:
// first "=" must be received then "\r" (CR)
// todo: timout, buffer full
#define TXBUF_LEN   32
// RX buffer is for usb-serial receive
#define RXBUF_LEN   32

// from RX deliver only packets containing valid chars 0:OFF 1:ON
#define VALID_CHARS_ONLY 1
// cancel TX->RX serial echo 0:OFF 1:ON
#define CANCEL_ECHO 1
// slow is 5V friendly
// limits slew rate to 8
#define SLOW 1

// debug prints
#if 0
#define DEBUG_PRINTLN(x)  Serial.println(x)
#define DEBUG_WRITE(x)    Serial.write(x)
#define DEBUG_WRITE2(x,y) Serial.write(x,y)
#else
#define DEBUG_PRINTLN(x)
#define DEBUG_WRITE(x)
#define DEBUG_WRITE2(x,y)
#endif

// Hardware LED already defined
//#define LED_BUILTIN 2
#define LED_ON  LOW
#define LED_OFF HIGH

/*********** BLUETOOTH LOW ENERGY ***********/

// #define BLE_NAME "SynScan_b1e5" // original devices have hex from WiFi MAC to BLE name
#define BLE_NAME "SynScan_BLE"

//#define BLE_NAME_SHORT "SynScan"

/*
    Video: https://www.youtube.com/watch?v=oCMOYS71NIU
    Based on Neil Kolban example for IDF: https://github.com/nkolban/esp32-snippets/blob/master/cpp_utils/tests/BLE%20Tests/SampleNotify.cpp
    Ported to Arduino ESP32 by Evandro Copercini

   Create a BLE server that, once we receive a connection, will send periodic notifications.
   The service advertises itself as: 6E400001-B5A3-F393-E0A9-E50E24DCCA9E
   Has a characteristic of: 6E400002-B5A3-F393-E0A9-E50E24DCCA9E - used for receiving data with "WRITE"
   Has a characteristic of: 6E400003-B5A3-F393-E0A9-E50E24DCCA9E - used to send data with  "NOTIFY"

   The design of creating the BLE server is:
   1. Create a BLE Server
   2. Create a BLE Service
   3. Create a BLE Characteristic on the Service
   4. Create a BLE Descriptor on the characteristic
   5. Start the service.
   6. Start advertising.

   In this example rxValue is the data received (only accessible inside that function).
   And txValue is the data to be sent, in this example just a byte incremented every second.

   16-bit Attribute UUID replaces the x’s in the following:
   0000xxxx-0000-1000-8000-00805F9B34FB

   32-bit Attribute UUID replaces the x's in the following:
   xxxxxxxx-0000-1000-8000-00805F9B34FB

   hcitool lescan

   https://github.com/Jakeler/ble-serial
   source ble-venv/bin/activate
   ble-scan -i hci1
   Started general BLE scan
   24:0A:C4:11:22:33 (rssi=-48): SynScan_BLE
   ble-serial -i hci1 -d 24:0A:C4:11:22:33
*/
#include <BLEDevice.h>
#include <BLEServer.h>
#include <BLEUtils.h>
#include <BLE2902.h>

BLEServer *pServer = NULL;
BLECharacteristic *pTxCharacteristic;
BLECharacteristic *pRxCharacteristic;

// default is 15 normally we don't need more
#define BLE_HANDLERS 15

// direction mount->synscan
// enable one of:
// NOTIFY   faster, no required confirmation from other end
// INDICATE slower, requires confirmation from other end
// synscan works only with TX_INDICATE
#define TX_NOTIFY   0
#define TX_INDICATE 1


// direction synscan->mount
// enable one or none
// if CHARACTERISTIC_UUID_TXRX is used and RX_NOTIFY is enabled
// then android serial bluetooth terminal prints repeated chars
// maybe comm is not fully correct with RX_NOTIFY with TXRX
// if notify is not enabled, synscan will keep on sending the same message
// for 1 second
// synscan works only with RX_NOTIFY
#define RX_NOTIFY   1
#define RX_INDICATE 0

bool rx_indicate = false;
bool deviceConnected = false;
bool oldDeviceConnected = false;

uint8_t txbuf[TXBUF_LEN+2], rxbuf[RXBUF_LEN+2]; // +2 to terminate with \n\0 for debug priting
uint32_t txbuf_index = 0, rxbuf_index = 0;
int32_t prev_rj12_rx_us = 0;
int32_t next_rj12_tx_us = 0;
int32_t next_usb_rx_us = 0;
uint8_t txbuf_acceptable[256], rxbuf_acceptable[256];
bool expect_fw_version = false;
bool rewrite_aux_encoder = false;
bool response_detected = false;

// See the following for generating UUIDs:
// https://www.uuidgenerator.net/

#if 0
// serial terminal works
#define SERVICE_UUID           "6E400001-B5A3-F393-E0A9-E50E24DCCA9E"  // UART service UUID nordic nRF
#define CHARACTERISTIC_UUID_RX "6E400002-B5A3-F393-E0A9-E50E24DCCA9E"
#define CHARACTERISTIC_UUID_TX "6E400003-B5A3-F393-E0A9-E50E24DCCA9E"
#endif
#if 0
// serial terminal works
#define SERVICE_UUID             "0000ffe0-0000-1000-8000-00805f9b34fb"  // UART service UUID Telit TIO
#define CHARACTERISTIC_UUID_TXRX "0000ffe1-0000-1000-8000-00805f9b34fb"
#endif
#if 0
// serial terminal works
#define SERVICE_UUID           "49535343-FE7D-4AE5-8FA9-9FAFD205E455"  // UART service UUID microchip RN4871
#define CHARACTERISTIC_UUID_RX "49535343-8841-43F4-A8D4-ECBE34729BB3"
#define CHARACTERISTIC_UUID_TX "49535343-1E4D-4BD9-BA61-23C647249616"
#endif
#if 1
// synscan works
#define SERVICE_UUID             "0000a002-0000-1000-8000-00805F9B34FB"  // SynScan has 
#define CHARACTERISTIC_UUID_RX   "0000c302-0000-1000-8000-00805F9B34FB"  // SynScan->Mount 0xc302 WRITE
#define CHARACTERISTIC_UUID_TX   "0000c306-0000-1000-8000-00805F9B34FB"  // Mount->SynScan 0xc306 INDICATE
#endif
#if 0
// serial terminal doesn't work "gatt status 133"
#define SERVICE_UUID           "0000fefb-0000-1000-8000-00805f9b34fb"  // UART service UUID Telit TIO
#define CHARACTERISTIC_UUID_RX "00000002-0000-1000-8000-00805f9b34fb"
#define CHARACTERISTIC_UUID_TX "00000001-0000-1000-8000-00805f9b34fb"
#endif

// ManufacturerData makes BLE device appear
// in connect list on android synscan pro 2.5.2

// on windows synscan 2.5.2 BLE device will appear
// on the connect list regardless of ManufacturerData

// first 2 bytes "h." (hex 0x68 0x2e)
// in nRF connect appear as
// Company: Reserved ID: <0x2E68>
// following 4 bytes encode string "54806524"
// in nRF connect appear as
// 0x3534383036353234
// ghydra found it:
// void FUN_140137c80(longlong *param_1)
// this = (QByteArray *)QBluetoothDeviceInfo::manufacturerData(pQVar7,local_90,0x2e68);
// pcStack_50 = QByteArrayView::castHelper("54806524");
#define ManufacturerData "h.54806524"

// see https://esp32.com/viewtopic.php?t=16492
BLEAdvertisementData oAdvertisementData = BLEAdvertisementData();

// *********** COMMON CODE **************
void (*loop_selected)(void); // pointer to loop function BT or BLE

class MyServerCallbacks : public BLEServerCallbacks
{
  void onConnect(BLEServer *pServer)
  {
    deviceConnected = true;
    digitalWrite(LED_BUILTIN, LED_ON);  // turn the LED on
  };

  void onDisconnect(BLEServer *pServer)
  {
    deviceConnected = false;
    digitalWrite(LED_BUILTIN, LED_OFF);  // turn the LED off
  }
};

class MyCallbacks : public BLECharacteristicCallbacks
{
  void onWrite(BLECharacteristic *pCharacteristic)
  {
    //Serial.println("\nwrite");
    String rxValue = pCharacteristic->getValue();
    #if 0
    if (rxValue.length() > 0)
    {
      digitalWrite(LED_BUILTIN, LED_OFF);  // turn the LED off
      for (int i = 0; i < rxValue.length(); i++)
      {
        Serial2.write(rxValue[i]);
        DEBUG_WRITE(rxValue[i]);
        delay(1);
      }
    }
    #else
    if (rxValue.length() > 0)
    {
      digitalWrite(LED_BUILTIN, LED_OFF);  // turn the LED off
      expect_fw_version = rxValue == ":e1\r";
      if(rxValue == "AT+CWMODE_CUR?\r\n") // this is problematic command
      {
        Serial2.write(":e1\r"); // rewritten as non-problematic command :e1
        DEBUG_WRITE2(rxValue.c_str(), rxValue.length());
      }
      // fix for virtuoso heritage 90 with firmware v2.16.A1
      // problem: mount turns non stop if auxiliary encoders are not used
      // this rewrites :W2050000\r -> :W2040000\r
      // now it is not neccessary to enable auxiliary encoders
      else if(rewrite_aux_encoder && rxValue == ":W2050000\r") // this is problematic command
      {
        Serial2.write(":W2040000\r"); // rewritten as non problematic command
        DEBUG_WRITE2(rxValue.c_str(), rxValue.length());
      }
      #if SLOW
      // prevent reboots at 5V power
      // MANUAL SLEW SPEED
      // instead of manual slew 9 use slew 8.5
      else if(rewrite_aux_encoder && rxValue == ":I1500000\r") // AZ manual speed 9
      {
        Serial2.write(":I1600000\r"); // rewritten as AZ manual speed 8.5
        DEBUG_WRITE2(rxValue.c_str(), rxValue.length());
      }
      else if(rewrite_aux_encoder && rxValue == ":I2500000\r") // ALT manual speed 9
      {
        Serial2.write(":I26000000\r"); // rewritten as ALT manual speed 8.5
        DEBUG_WRITE2(rxValue.c_str(), rxValue.length());
      }
      // GOTO SLEW SPEED
      // M-commands (brake) don't have any effect
      // replace them with long goto slew 8.5
      else if(rewrite_aux_encoder && rxValue == ":M1AC0D00\r") // AZ brake
      {
        Serial2.write(":T1600000\r"); // rewritten as AZ long goto speed 8
        DEBUG_WRITE2(rxValue.c_str(), rxValue.length());
      }
      else if(rewrite_aux_encoder && rxValue == ":M2AC0D00\r") // ALT brake
      {
        Serial2.write(":T2600000\r"); // rewritten as ALT long goto speed 8
        DEBUG_WRITE2(rxValue.c_str(), rxValue.length());
      }
      #endif // SLOW
      else
      {
        Serial2.write(rxValue.c_str(), rxValue.length());
        DEBUG_WRITE2(rxValue.c_str(), rxValue.length());
      }
    }
    #endif
    #if RX_NOTIFY
    pCharacteristic->notify();
    #endif
    #if RX_INDICATE
    rx_indicate = true;
    #endif
    DEBUG_WRITE('\n');
  }
};

void reset_txbuf()
{
  txbuf_index = 0;
  response_detected = false;
}

void reset_rxbuf()
{
  rxbuf_index = 0;
}

void init_txbuf_acceptable()
{
  memset(txbuf_acceptable    , 0, 256); // clear
  txbuf_acceptable['='] = 1;
  memset(txbuf_acceptable+'0', 1, 10); // 0-9 set as acceptable
  memset(txbuf_acceptable+'A', 1, 6); // A-F set as acceptable
  txbuf_acceptable['\r'] = 1;
}

void init_rxbuf_acceptable()
{
  memset(rxbuf_acceptable    , 0, 256); // clear
  rxbuf_acceptable[':'] = 1;
  rxbuf_acceptable['!'] = 1;
  memset(rxbuf_acceptable+'0', 1, 10); // 0-9 set as acceptable
  memset(rxbuf_acceptable+'A', 1, 26); // A-Z set as acceptable
  memset(rxbuf_acceptable+'a', 1, 26); // a-z set as acceptable
  rxbuf_acceptable['\r'] = 1;
}

void init_usb_timing()
{
  // reset serial time tracking
  int32_t time_us = micros();
  prev_rj12_rx_us = time_us;
  next_rj12_tx_us = time_us;
  next_usb_rx_us  = time_us;
}

void setup_ble()
{
  Serial.begin(); // on ESP32S3 this is usb-serial
  Serial2.begin(BAUD, SERIAL_8N1, RXD2, TXD2);

  // Create the BLE Device
  BLEDevice::init(BLE_NAME);

  // Create the BLE Server
  pServer = BLEDevice::createServer();
  pServer->setCallbacks(new MyServerCallbacks());

  // Create the BLE Service
  BLEService *pService = pServer->createService(BLEUUID(SERVICE_UUID), BLE_HANDLERS);

  #ifdef CHARACTERISTIC_UUID_TXRX
  // one characteristic for both RX and TX
  // Create a BLE Characteristic
  pTxCharacteristic = pService->createCharacteristic(
    CHARACTERISTIC_UUID_TXRX,
  #if TX_NOTIFY
    BLECharacteristic::PROPERTY_NOTIFY |
  #endif
  #if TX_INDICATE
    BLECharacteristic::PROPERTY_INDICATE |
  #endif
    BLECharacteristic::PROPERTY_WRITE);
  pTxCharacteristic->addDescriptor(new BLE2902());
  pTxCharacteristic->setCallbacks(new MyCallbacks());
  #else
  // separate characteristics for RX and TX
  auto DescriptorTx2902 = new BLE2902();
  // Create a BLE Characteristic
  #if TX_NOTIFY
  pTxCharacteristic = pService->createCharacteristic(CHARACTERISTIC_UUID_TX, BLECharacteristic::PROPERTY_NOTIFY);
  DescriptorTx2902->setNotifications(true);
  #else
  DescriptorTx2902->setNotifications(false);
  #endif
  #if TX_INDICATE
  pTxCharacteristic = pService->createCharacteristic(CHARACTERISTIC_UUID_TX, BLECharacteristic::PROPERTY_INDICATE);
  DescriptorTx2902->setIndications(true);
  #else
  DescriptorTx2902->setIndications(false);
  #endif
  // in nRF connect BLE2902 appears under
  // TX Characteristic
  // Descriptors:
  // Client Characteristic Configuration
  // UUID: 0x2902
  pTxCharacteristic->addDescriptor(DescriptorTx2902);

  BLEDescriptor *DescriptorRx2901 = new BLEDescriptor("2901");
  #if RX_NOTIFY
  //DescriptorRx2901->setNotifications(true);
  #else
  //DescriptorRx2901->setNotifications(false);
  #endif
  #if RX_INDICATE
  //DescriptorRx2901->setIndications(true);
  #else
  //DescriptorRx2901->setIndications(false);
  #endif
  pRxCharacteristic = pService->createCharacteristic(CHARACTERISTIC_UUID_RX, BLECharacteristic::PROPERTY_WRITE);
  // in nRF connect BLE2902 appears under
  // RX Characteristic
  // Descriptors:
  // Client Characteristic Configuration
  // UUID: 0x2902
  //pRxCharacteristic->addDescriptor(DescriptorRx2902);
  // Characteristic User Description
  // UUID: 0x2901
  pRxCharacteristic->addDescriptor(DescriptorRx2901);
  pRxCharacteristic->setCallbacks(new MyCallbacks());
  #endif

  BLEAdvertising *pAdvertising = BLEDevice::getAdvertising();
  pAdvertising->addServiceUUID(SERVICE_UUID);
  pAdvertising->setScanResponse(true);
  #ifdef BLE_NAME_SHORT
  oAdvertisementData.setShortName(BLE_NAME_SHORT);
  #endif
  oAdvertisementData.setManufacturerData(ManufacturerData);
  pAdvertising->setAdvertisementData(oAdvertisementData);
  pAdvertising->setMinPreferred(0x06);  // functions that help with iPhone connections issue
  pAdvertising->setMinPreferred(0x12);

  // Start the service
  pService->start();

  // control the LED
  pinMode(LED_BUILTIN, OUTPUT);

  // setup detailed advertising response

  // Start advertising
  pAdvertising->start();
  DEBUG_WRITE("Bluetooth Low Energy Serial: ");
  DEBUG_PRINTLN(BLE_NAME);
  init_txbuf_acceptable();
  init_rxbuf_acceptable();
  init_usb_timing();
}

void loop_ble()
{
  uint8_t txValue, rxValue;
  int32_t time_us;
  static bool txbuf_complete_for_delivery = true, rxbuf_complete_for_delivery = true;

  // RJ-12 serial read
  time_us = micros();
  if(Serial2.available())
  {
    digitalWrite(LED_BUILTIN, LED_OFF);  // turn the LED on
    txValue = Serial2.read();
    if(txValue == '=' || txValue == '!')
    {
      response_detected = true;
      #if CANCEL_ECHO
      txbuf_index = 0;
      #endif
    }
    txbuf[txbuf_index++] = txValue;
    txbuf_complete_for_delivery = txbuf_index >= TXBUF_LEN || (response_detected && txValue == '\r');
    if(txbuf_complete_for_delivery)
    {
      // deliver data now
      if(deviceConnected)
        pTxCharacteristic->setValue(txbuf, txbuf_index); // txbuf_index is the length
      if(expect_fw_version)
        rewrite_aux_encoder = memcmp(txbuf,"=0210A1\r",txbuf_index) == 0;
      Serial.write(txbuf, txbuf_index); // usb-serial
      // reset after delivery, prepare for next data
      reset_txbuf();
      #if TX_NOTIFY
      if(deviceConnected)
        pTxCharacteristic->notify();
      #endif
      #if TX_INDICATE
      if(deviceConnected)
        pTxCharacteristic->indicate();
      #endif
    }
    else // Packet not yet complete for delivery. Still in serial2 available,
    {
      #if VALID_CHARS_ONLY
      if(txbuf_acceptable[txValue] == 0)
        reset_txbuf();
      #endif
    }
    prev_rj12_rx_us = time_us;
  }
  else // RJ-12 Serial2 not available
  {
      if(time_us-prev_rj12_rx_us > RJ12_RX_TIMEOUT_US)
        reset_txbuf();
  }

  time_us = micros();
  // this tries to prevent TX2 while RX2 from sniffing the protocol
  // usb-serial is much faster than 9600
  // USB serial read
  if(Serial.available() && time_us-next_usb_rx_us > 0) // usb-serial read at limited rate, throttle r12-write
  {
    rxValue = Serial.read();
    if(rxValue == ':')
      reset_rxbuf();
    rxbuf[rxbuf_index++] = rxValue;
    rxbuf_complete_for_delivery = rxbuf_index >= RXBUF_LEN ||
    ( (rxbuf[0] == ':' && rxValue == '\r') || rxValue == '\n' );
    if(rxbuf_complete_for_delivery)
    {
      // code here has same function as the BLECharacteristicCallbacks with String
      // but because of rxbuf and memcmp it is written differently
      // todo unify both
      if(time_us-next_rj12_tx_us > 0) // discards packets coming too fast
      {
        expect_fw_version = memcmp(rxbuf, ":e1\r", rxbuf_index) == 0;
        if(memcmp(rxbuf, "AT+CWMODE_CUR?\r\n", rxbuf_index) == 0) // this is problematic command
          Serial2.write(":e1\r"); // rewritten as non-problematic command :e1
        else if(rewrite_aux_encoder && memcmp(rxbuf, ":W2050000\r", rxbuf_index) == 0) // this is problematic command
          Serial2.write(":W2040000\r"); // rewritten as non problematic command
        #if SLOW
        // prevent reboots at 5V power
        // MANUAL SLEW SPEED
        // instead of manual slew 9 use slew 8.5
        else if(rewrite_aux_encoder && memcmp(rxbuf, ":I1500000\r", rxbuf_index) == 0) // AZ manual speed 9
          Serial2.write(":I1600000\r"); // rewritten as AZ manual speed 8
        else if(rewrite_aux_encoder && memcmp(rxbuf, ":I2500000\r", rxbuf_index) == 0) // ALT manual speed 9
          Serial2.write(":I2600000\r"); // rewritten as ALT manual speed 8
        // GOTO SLEW SPEED
        // M-commands (brake) don't have any effect
        // replace them with long goto slew 8.5
        else if(rewrite_aux_encoder && memcmp(rxbuf, ":M1AC0D00\r", rxbuf_index) == 0) // AZ brake
          Serial2.write(":T1600000\r"); // rewritten as AZ long goto speed 8
        else if(rewrite_aux_encoder && memcmp(rxbuf, ":M2AC0D00\r", rxbuf_index) == 0) // ALT brake
          Serial2.write(":T2600000\r"); // rewritten as ALT long goto speed 8
        #endif // SLOW
        else
          Serial2.write(rxbuf, rxbuf_index);
      }
      #if 1
      else
        Serial.write("\r"); // response to discarded packet
      #endif
      reset_rxbuf();
      next_rj12_tx_us += RJ12_TX_PACKET_US;
      time_us = micros();
      if(next_rj12_tx_us < time_us)
        next_rj12_tx_us = time_us + RJ12_TX_PACKET_US;
    }
    else // rxbuf not yet complete for delivery
    {
      #if VALID_CHARS_ONLY
      if(rxbuf_acceptable[rxValue] == 0)
        reset_rxbuf();
      #endif
    }
    next_usb_rx_us += USB_RX_CHAR_US;
    time_us = micros();
    if(next_usb_rx_us < time_us)
      next_usb_rx_us = time_us + USB_RX_CHAR_US;
  }
  else // usb Serial not available
  {
    if(time_us-next_usb_rx_us > USB_RX_TIMEOUT_US)
      reset_rxbuf();
  }

  #if RX_INDICATE
  if(deviceConnected)
    if(rx_indicate)
    {
      pRxCharacteristic->indicate();
      rx_indicate = false;
    }
  #endif

  // disconnecting
  if (!deviceConnected && oldDeviceConnected)
  {
    delay(500);                   // give the bluetooth stack the chance to get things ready
    pServer->startAdvertising();  // restart advertising
    DEBUG_PRINTLN("Disconnected");
    oldDeviceConnected = deviceConnected;
    // reset connection tracking states
    rx_indicate = false;
    reset_txbuf();
  }
  // connecting
  if (deviceConnected && !oldDeviceConnected)
  {
    // do stuff here on connecting
    oldDeviceConnected = deviceConnected;
    DEBUG_PRINTLN("Connected");
    // reset connection tracking states
    rx_indicate = false;
    reset_txbuf();
  }
  digitalWrite(LED_BUILTIN, (deviceConnected | ((((time_us>>16) & 15) == 0)) ) ^ LED_OFF); // disconnected: blink, connected: on
}


// This example code is in the Public Domain (or CC0 licensed, at your option.)
// By Evandro Copercini - 2018
//
// This example creates a bridge between Serial and Classical Bluetooth (SPP)
// and also demonstrate that SerialBT have the same functionalities of a normal Serial
// Note: Pairing is authenticated automatically by this device

// Check if Bluetooth is available
#if 0
#if !defined(CONFIG_BT_ENABLED) || !defined(CONFIG_BLUEDROID_ENABLED)
#error Bluetooth is not enabled! Please run `make menuconfig` to and enable it
#endif
#endif

// Check Serial Port Profile
#if 0
#if !defined(CONFIG_BT_SPP_ENABLED)
#error Serial Port Profile for Bluetooth is not available or not enabled. It is only available for the ESP32 chip.
#endif
#endif


/************ COMMON ***********/
void setup()
{
  pinMode(LED_BUILTIN, OUTPUT);
  digitalWrite(LED_BUILTIN, LED_OFF);
  setup_ble();
  loop_selected = loop_ble;
}

void loop()
{
  (*loop_selected)();
}

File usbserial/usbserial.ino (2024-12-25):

// install Board -> Boards Manager -> "esp32 by espressif"
// Board: XIAO_ESP32S3
// CPU freq 80MHz (WiFi/BT) for power saving

// works for linux wine synscan
// doesn't work for android synscan

/*********** COMMON ***********/

// Hardware Serial2 pins
#define RXD2 44
#define TXD2 43
#define BAUD 9600

#define USB_RX_US 1042
#define RECEIVE_US 50000

#define CANCEL_ECHO 0

// Hardware LED already defined
//#define LED_BUILTIN 2
#define LED_ON  LOW
#define LED_OFF HIGH

int32_t prev_usb_rx_us;
int32_t prev_transmit_false_us;

void setup()
{
  Serial.begin(BAUD); // on ESP32S3 this is usb-serial
  Serial2.begin(BAUD, SERIAL_8N1, RXD2, TXD2);

  // control the LED
  pinMode(LED_BUILTIN, OUTPUT);

  digitalWrite(LED_BUILTIN, LED_ON);

  int32_t time_us = micros();
  prev_usb_rx_us = time_us;
  prev_transmit_false_us = micros();
}

void loop()
{
  uint8_t usb_rx, rj12_rx;
  int32_t time_us;
  static bool halt = false;
  static bool transmit = true;
  static bool response = false;

  time_us = micros();
  if(Serial2.available() && transmit == false)
  {
    rj12_rx = Serial2.read();
    if(rj12_rx == '=')
    {
      response = true;
      prev_transmit_false_us = time_us;
      digitalWrite(LED_BUILTIN, LED_OFF);
    }
    #if CANCEL_ECHO
    if(response)
    #endif
      Serial.write(rj12_rx);
    if(rj12_rx == '\r' && response == true)
    {
      response = false;
      transmit = true;
      while(Serial2.available())
        Serial2.read();
      digitalWrite(LED_BUILTIN, LED_ON);
    }
  }
  time_us = micros();
  if(Serial.available() && time_us-prev_usb_rx_us > USB_RX_US && transmit == true)
  {
    usb_rx = Serial.read();
    Serial2.write(usb_rx);
    if(usb_rx == '\r')
    {
      transmit = false;
      prev_transmit_false_us = time_us;
      while(Serial.available())
        Serial.read();
    }
    prev_usb_rx_us += USB_RX_US;
    time_us = micros();
    if(prev_usb_rx_us < time_us)
      prev_usb_rx_us = time_us;
  }

  if(transmit == false)
    if(time_us-prev_transmit_false_us > RECEIVE_US)
    {
      transmit = true;
      response = false;
    }
    
}

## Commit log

2024-11-09 it works from android serial terminal but synscan won't connect to this
    [blesynscan.ino]
2024-11-09 blink LED
2024-11-10 boot selectable BT or BLE serial. BT is default and it works from linux. BLE doesn't work yet for SynScan pro android.
    [btblesynscan.ino]
2024-11-18 android synscan pro 2.5.2 shows device name "SynScan_BLE" in the list but doesn't connect.
    [btblesynscan.ino]
2024-11-25 swap rx tx lines, comment what they do
    [btblesynscan.ino]
2024-11-28 commented code to advertise service uuid this line doesn't make difference in nrf connect view of device advertisement data
    [btblesynscan.ino]
2024-11-28 one step further, write is successful and sends data to the mount, mount responds but android seems as it doesn't get the response so no connect yet.
    [btblesynscan.ino]
2024-11-28 protocol seems to flow bidirectional now but still we are geting unexpected response and no connect
2024-11-28 cleanup, protocol seems to flow but no connect yet
2024-11-28 when every command starting with ":" is rewritten as ":e1" then it connects in AZ mode, but in this case mount doesn't work
    [btblesynscan.ino]
2024-11-29 fix AT rewrite, typo in multiple if/else
    [btblesynscan.ino]
2024-11-29 small comments and debug prints
2024-11-29 boards manager
2024-11-29 more readme, openscad project for 3D printable box
    [esp32synscan.scad]
2024-11-30 cleanup old code, comment to compile CPU frequency of 80 MHz for power saving.
2024-11-30 after connect/disconnect reset BLE connection tracking states
    [btblesynscan.ino]
2024-12-01 reset BLE receive buffer on timeout 10 ms
    [btblesynscan.ino]
2024-12-01 filter out only acceptable chars uart seems to often send garbled data with some bits having tendency to become 1 instead of 0. Maybe weak electrical signal?
2024-12-01 board pic's
2024-12-01 readme pictures of the board
2024-12-01 noise reduction options and seems 9800 baud works slightly more reliable than 9600
    [btblesynscan.ino]
2024-12-07 revert speed to 9600 after putting schottky diode BAT42 in series with TX. This diode simulates open collector TX.
    [btblesynscan.ino]
2024-12-08 simple diode symbol maybe renders better
2024-12-08 readme schematics updated with 10k pullup to 3.3V
2024-12-12 esp32-s3 version, visible on BLE list but untested
2024-12-21 readme preparation for ESP32S3
2024-12-21 RJ12 socket turned around now it is in the same position as on the mount
2024-12-21 ESP32S3 schematics
2024-12-22 usb-serial bridge, works for linux wine synscan doesn't work for android
    [esp32s3.ino]
2024-12-22 esp32s3 3D printable box
    [esp32s3synscan.scad]
2024-12-22 create esp32 directory and move projects there
2024-12-22 readme cleanup, update for ESP32S3
2024-12-22 readme simplyfied ESP32S3 schematics
2024-12-22 readme aboud USB-SERIAL wired connection.
2024-12-22 esp32 usb-serial, works on linux wine synscan doesn't work on android
    [btblesynscan.ino]
2024-12-22 better rails for esp32s3 box
    [esp32s3synscan.scad]
2024-12-22 box for RJ-12 connector top socked (hole on box side)
    [esp32s3synscan.scad]
2024-12-22 expect find firmware version, for specific value "=0210A1\r" apply bugfix rewriting aux encoder command
    [esp32s3.ino]
2024-12-22 easier insertion, allow space for solder points
    [esp32s3synscan.scad]
2024-12-23 readme update filter noise and reconnect
2024-12-23 BLE LED disconnected: blink, connected: on
2024-12-23 compile time option "CANCEL_ECHO", rename "NOISE_REDUCTION" -> "VALID_CHARS_ONLY" self-descriptive
    [esp32s3.ino]
2024-12-23 usb-serial in the same loop as BLE. currently packet rewriting is not done for usb-serial. usb-serial on linux wine works ok.
    usb-serial on android connects but it is unreliable,
    data garbled, probably collistions doing TX while RX.
2024-12-23 trying to fix android usb-serial, still not ok
    [esp32s3.ino]
2024-12-24 trying to fix android usb-serial with timeouts but still garbage in serial
    [esp32s3.ino]
2024-12-24 present release, android usb-serial not working good
    [esp32s3.ino]
2024-12-25 usbserial example, works for linux wine synscan doesn't work for android
    [usbserial.ino]
2024-12-25 various tricks applied trying to fix protocol for android but not much can be done. Best option is to disable throttling cancel echo and let only packets with valid chars pass
    [esp32s3.ino]
2024-12-27 RJ-12 RJ-11 sockets part numbers
2024-12-27 connector pinout
2024-12-27 esp32 TX/RX signal direction
2024-12-27 12V power direction indicated
2025-01-02 pic of esp32s3
2025-03-25 binary esp32 esp32s3
2025-07-02 micropython: slow speed option is 5V friendly
2025-07-02 esp32s3: 5V friendly and quiet: limit speed from 9 to 8
2025-07-02 esp32s3 binary
2025-07-25 instead of speed 8 use speed 8.5 a bit faster and still 5V friendly
2025-09-14 pinouts for mini and GTi GTi currently doesn't work.
2025-09-17 optional Virtuoso AZ encoder fix
2025-09-19 micropython slow speed to prevent main encoders loosing counts
2025-09-20 micropython different speeds for main and aux encoders
2025-09-21 micropythonc cleanup details limit udp tx/rx to 32 chars, blink led
2025-09-21 micropython cfg encoders 0:main/aux 1:main 2:aux
2025-09-21 micropython if e1 (get fw version) is unsuccessful, try wire_autodetect()
2025-09-21 micropython wifi timer led update
2025-09-21 wifi mode doesn't like uart audotect while trying to connect
    [synscan.py]
2025-10-11 GTi: correcting wrong counts per revolution
    [synscan.py]
2025-10-11 configurable dictionary replacement of commands and responses
    [synscan.py]
2025-10-11 duplex autodetect bug fixed (wrong identation)
    [synscan.py]
2025-10-11 print trying duplex
2025-10-12 print AT commands for debugging
2025-10-13 wifi setting tx power
2025-10-15 reporting firmware version 2.16.A1 seems to fix aux encoders because synscan will use E and F initialization commands during connect phase
2025-10-15 reverting to 2.16.A1 and using E and F doesn't fix aux encoders on firmware 3.40.AF. After few minutes of woring with aux encoders mount will loose position and go "crazy"
2025-10-16 readme aux encoders
2025-10-26 pic of motor worm wheel transmission
2025-10-26 backlash text improved
2025-10-26 baclash describe black screw
2025-11-08 wifi ap: print IP immediately wifi client: print IP when connected
2025-11-09 ble remote connection, currently only TX works, RX doesn't
2025-11-09 wip: wifi client example, connects but doesn't work
    [wifiremote.py]
2025-11-09 wifiremote.py works for esp32c3
2025-11-10 commented led pin for esp32 devikit
2025-11-10 esp32c3 pinout
2025-11-10 new code esp32c3 as wifi client when typing commands like :e1 it works but synscan won't connect
    [synscan.py]
2025-11-11 moving files to Arduino directory and update readme's
2025-11-11 support wired usb-serial, untested
2025-11-11 synscan.py usbserial fix typo wire_txrx() -> wire_txrx_replace()
    [synscan.py]
2025-11-12 print quick help in main.py
2025-11-13 synscan_cfg.py example for direct wire usb-serial
2025-11-16 new box for C3/S3
    [esp32s3synscan.scad]
2025-11-16 micropython ESP32S3: fix to connect as client
    [synscan.py]
2025-11-16 S3 fix for WiFi connect: reduce txpower=17 -> txpower=15
    [synscan.py]
2025-12-13 reduce tx power otherwise wifi won't connect increase timeout to 2 seconds
    [synscan.py]
